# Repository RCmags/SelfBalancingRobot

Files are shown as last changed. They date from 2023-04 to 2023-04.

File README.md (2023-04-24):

# Controller for self-balancing robot :aerial_tramway:
This is an arduino sketch for an inverted pendulum with two wheels (a [self balancing robot](https://people.ece.cornell.edu/land/courses/ece4760/FinalProjects/f2015/dc686_nn233_hz263/final_project_webpage_v2/dc686_nn233_hz263/index.html)). Due to the unstable nature of this platform, it must be actively stabilized to maintain balance.

## Operation
The program provides stabilization through an MPU6050 IMU and two brushed DC motors driven by an H-bridge. It uses three PID loops acting simultaneously:

- __Pitch stabilization:__ This is the dominant PID controller of the system. It uses the pitch angle of the vehicle as a proportional term to keep the vehicle upright by accelerating into gravity. 

- __Position stabilization:__ It estimates the velocity by integrating pitch angle, which is proportional to the _lateral acceleration_ (at small angles), and this is integrated again to approximate _position_ (the double integral of the pitch angle). Both are used as the derivative and proportional term respectively. Their combined effect prevent the vehicle from drifting laterally and counters any change in center of gravity.  

<p align="center">
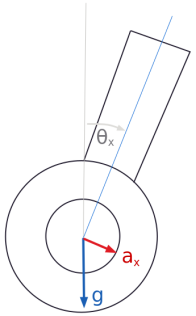
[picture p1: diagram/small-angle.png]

</p>

$$ a_x \propto \theta_x $$

$$ v_x = \int{a_x}dt \propto \int{ \theta_x dt } $$

$$ x = \int{v_x}dt \propto \int{ \int{ \theta_x dt^2 } } $$

- __Yaw stabilization:__ A controller that maintains heading by using as a proportional term the angular velocity of the yaw axis. It counters the open-loop nature of the motor control, wherein one motor can spin faster and cause the vehicle to turn.

Ultimately, the unstable axis is only stabilized by the measured pitch angle. 

__Note:__ Both motors are driven with _pulse frequency modulation_ to counter magnetic cogging and stiction. The duty is cycle is long enough so that each pulse causes the motors to rotate one magnetic pole. Such a waveform provides precise control over low-speed rotation at the cost of jerky movement. This precision is necessary to reduce under and over correction when the vehicle is nearly vertical. 

Driving the motors like this causes them to behave similar to a stepper motor, albeit with much less precision, larger steps, and less torque.  

## Dependencies
These are the libraries needed to compile this sketch:

- [basicMPU6050](https://github.com/RCmags/basicMPU6050)
- [imuFilter](https://github.com/RCmags/imuFilter)
- [pulseInput](https://github.com/RCmags/pulseInput)
- [TimerOne](https://github.com/PaulStoffregen/TimerOne)

## Schematic   
<p align="center">
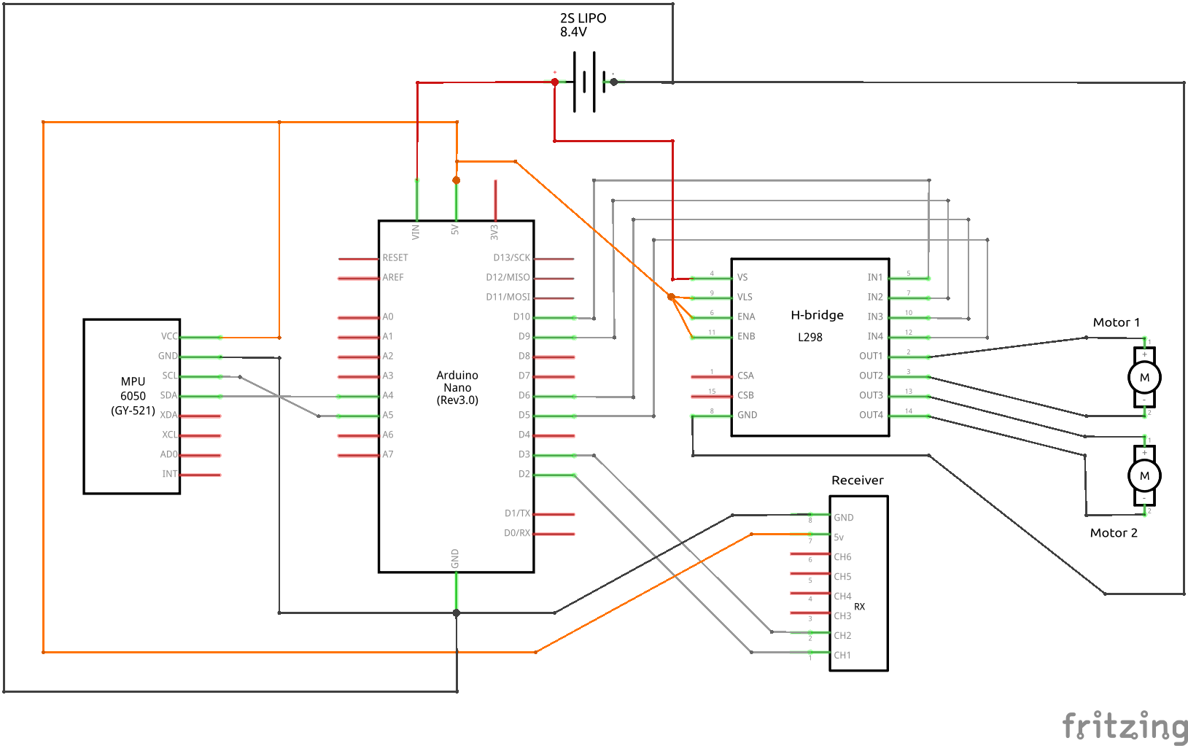
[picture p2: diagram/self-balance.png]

</p>

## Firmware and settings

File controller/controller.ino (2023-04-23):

/* Arduino NANO sketch to stabilize and control a self-balancing robot (similar to a segway).
 * It commands two DC motors via and h-bridge to rotate and translate the vehicle.
 * Author: RCmags https://github.com/RCmags
 * 
 * NOTE: 
 * This sketch uses an MPU6050 IMU (gyroscope and accelerometer) to stabilize pitch axis. It 
 * does so by constantly accelerating into the direction of tilt to remain upright.
 * 
 * Important! Check the header files to configure the controller. See the "parameters" sections.
*/

//=============== Connections ================
// See included schematic
  // Inputs:
// Pin 2  -> Receiver CH1
// Pin 3  -> Receiver CH2
// Pin A5 -> Sensor SCL
// Pin A4 -> Sensor SDA
  // Outputs:
// Pin 5  -> Left  motor pin
// Pin 6  -> Left  motor pin 
// Pin 9  -> Right motor pin
// Pin 10 -> Right motor pin

//=================== Code ===================
#include "fusion.h"
#include "hbridge.h"
#include "input.h"
#include "pid.h"

void setup() {     
  // RX signals
  setPwmInputs();
  delay(1000);      // allow receiver to initialize
  
  // Calibrate imu
  imu.setup();
  imu.setBias();
  fusion.setup( imu.ax(), imu.ay(), imu.az() );     

  // setup h-bridge
  setupPulses();
}

void loop() {
  // update attitude
  fusion.update( imu.gx(), imu.gy(), imu.gz(), imu.ax(), imu.ay(), imu.az(), GAIN, SD_ACCEL );  

  // get receiver inputs
  float input[2]; filterInputs(input);

  // set motors
  float rate[2]; PIDcontrollers(input, rate);
  motors.setRate(rate);
}

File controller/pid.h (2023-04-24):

//=========== PID stabilization ============
/* PID control loop to stabilize and steer the vehicle */

//=============== Parameters ===============

            // pitch
constexpr float KP_P = 5;       // Short-term spring constant:    Prevents vehicle from falling.
constexpr float KI_P = 40;      // Long-term spring constant:     Forces vehicle to stay upright.
constexpr float KD_P = 0.35;    // Angular damping:               Stabilizes KP_P. Slows down rotation.
            // position  
constexpr float KP_X = 4;       // Position:                      acts as spring constant. Increase to reduce displacement from C.G. changes.
constexpr float KD_X = 2.5;     // Velocity:                      softly damps the position spring. Cannot increase too much or causes diverging instability.  
            // yaw
constexpr float KP_Y = 0.3;     // Angular spring constant:       Use to maintain heading.  
constexpr float KD_Y = 0.05;    // Angular damping:               Prevents KP_Y from overshooting. Too much causes rapid jitter. 

//=============== Functions ================

float clamp(float x) {
  return constrain(x, -1, 1);
}

void PIDcontrollers( float input[], float output[] ) {
  // state [initialize at rest]
  static float vel = 0;
  static float pos = 0;
  
  // pid - position
  float dvel = vel - input[1];
  float pid_x = KP_X*pos + KD_X*dvel;
  
  // integrals
  float acc = fusion.pitch() + pid_x; // add position feedback
  
  float dt = fusion.timeStep();
  vel += acc * dt;
  vel = clamp(vel);

  pos += dvel * dt;
  pos = clamp(pos);

  // pid - pitch
  float pid_p = KP_P*acc + KI_P*vel + KD_P*imu.gy();   

  // pid - yaw
  fusion.rotateHeading( -input[0]*dt, SMALL_ANGLE);

  float dy = fusion.yaw() - 0.25*input[0];
  float pid_y = KP_Y*dy + KD_Y*imu.gz(); 

  // return rates
  output[0] = pid_p - pid_y;
  output[1] = pid_p + pid_y;
}

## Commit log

2021-08-22 schematic of vehicle
2023-04-23 update diagram
    [self-balance.fzz]
